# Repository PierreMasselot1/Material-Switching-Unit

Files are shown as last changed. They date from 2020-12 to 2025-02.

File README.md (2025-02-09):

                   

> ⚠️ **This repository has been archived and is no longer actively maintained.** ⚠️
> 
> While the Material Switching Unit (MSU) remains available for reference, please note that:
> - **No new updates, bug fixes, or features will be added.**
> - **Issues and pull requests are no longer monitored or accepted.**
> Use this project at your own discretion, and check the community for alternatives or forks if needed.

# Material Switching Unit (MSU)

The Material Switching Unit is a multi-material upgrade for 3D printers based on the MMU2 that allows printing of up to 5 filaments while staying under 80$ and being compatible with most FDM 3D printers out there.

# Getting started

Clone the repository using the following command (you will need [git](https://git-scm.com/downloads) on your machine)

`git clone --recursive https://github.com/PierreMasselot1/Material-Switching-Unit.git
`

Once this is done you should now have access to the different parts required for this project. The Marlin folder contains the modified firmware that will allow you to control the MSU and the parts forlder contains all the 3D files that you will need.

Have a look at the [build guide](https://github.com/PierreMasselot1/Material-Switching-Unit/blob/main/Build_guide_MSU.md) for further guidance on how to get the MSU up and running!

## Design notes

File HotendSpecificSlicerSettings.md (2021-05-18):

| Hotend Model+Type | E3D V6 (Bowden) | | | | | | | | |
| --- | --- | --- | --- | --- | --- | --- | --- | --- | --- |
| loading speed at the start | 19 | | | | | | | | |
| loading speed | 14 | | | | | | | | |
| unloading speed at the start | 120 | | | | | | | | |
| Unloading speed | 100 | | | | | | | | |
| Number of cooling moves & speed first and last (eg: 1,3,4) | 1,3,6 | | | | | | | | |
| cooling tube position | 40 | | | | | | | | |
| cooling tube length | 7 | | | | | | | | |
| Filament parking position | 70 | | | | | | | | |
| Extra loading distance | 0 | | | | | | | | |
| Important info | Needs Capricorn tubing <br> or PTFE with ID<=1.9mm | | | | | | | | |
| Ramming settings PLA (time: Volumetric speed mm^3/s) | 0.0: 4 / 0.6: 4 / 0.9: 5 / 1.5: 10 / 2: 11 | | | | | | | | |
| | | | | | | | | | |
| | | | | | | | | | |
| | | | | | | | | | |

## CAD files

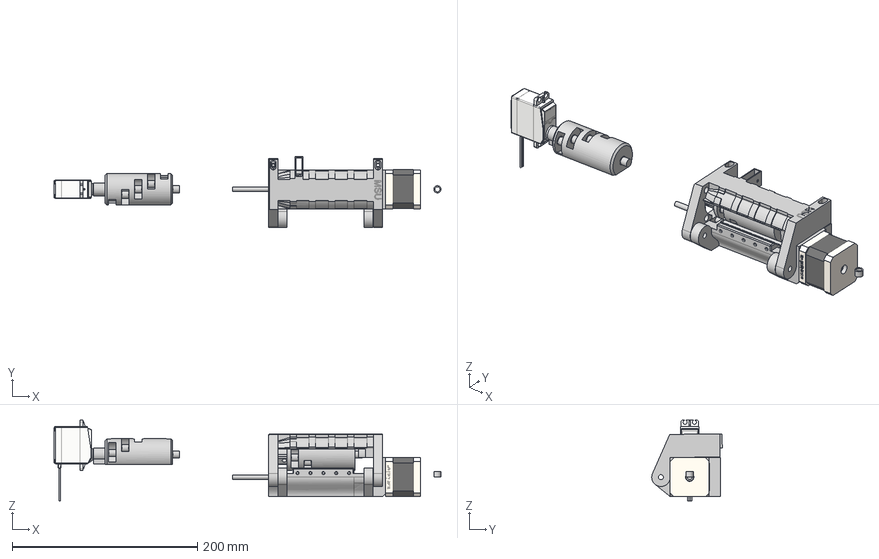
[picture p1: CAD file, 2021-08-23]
parts/STEP/MSU_assembly.step
417.4 x 76.1 x 87.2 mm
pulley body
Idler body stepper
Servo
Idler for servo
bearing adapter
idler stepper motor
Holder nema17 v1

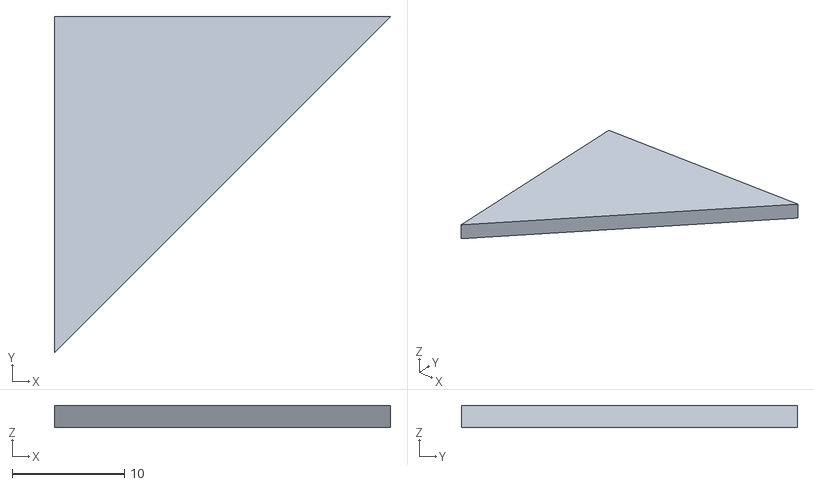
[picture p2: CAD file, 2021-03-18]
FilamentTipTesting/Body1.stl
30.0 x 30.0 x 2.00

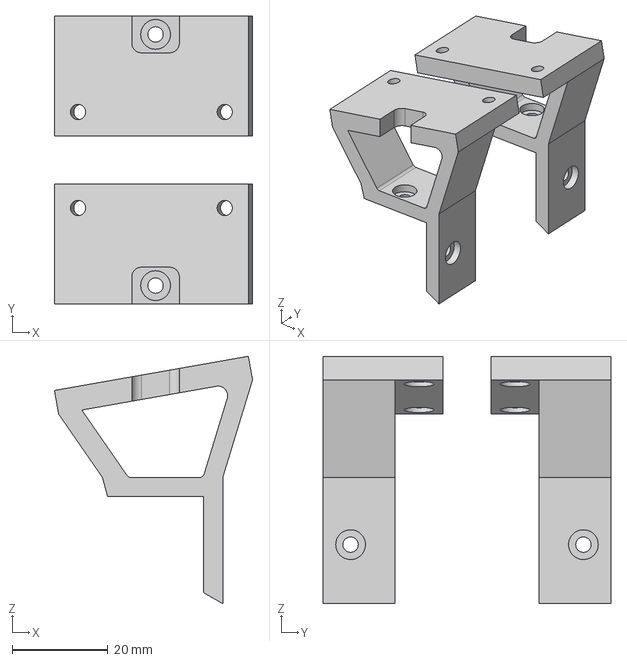
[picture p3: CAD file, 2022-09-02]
parts/STEP/Extrusion_mount.step
41.3 x 60.0 x 51.6 mm

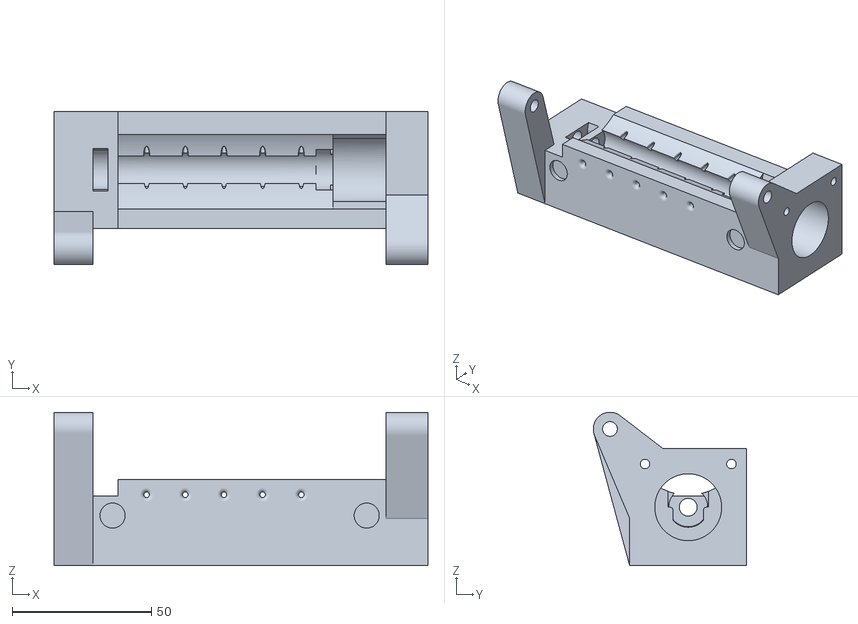
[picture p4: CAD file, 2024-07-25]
parts/STL/Experimental/new_pivot_pulley_body.stl
134.2 x 55.1 x 55.1

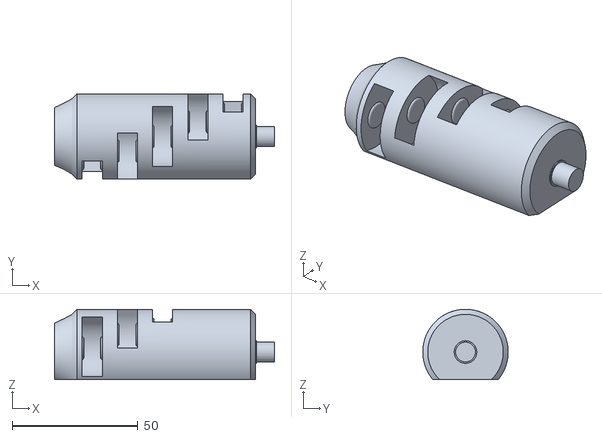
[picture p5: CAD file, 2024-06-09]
parts/STL/Idler.stl
87.5 x 34.0 x 28.0

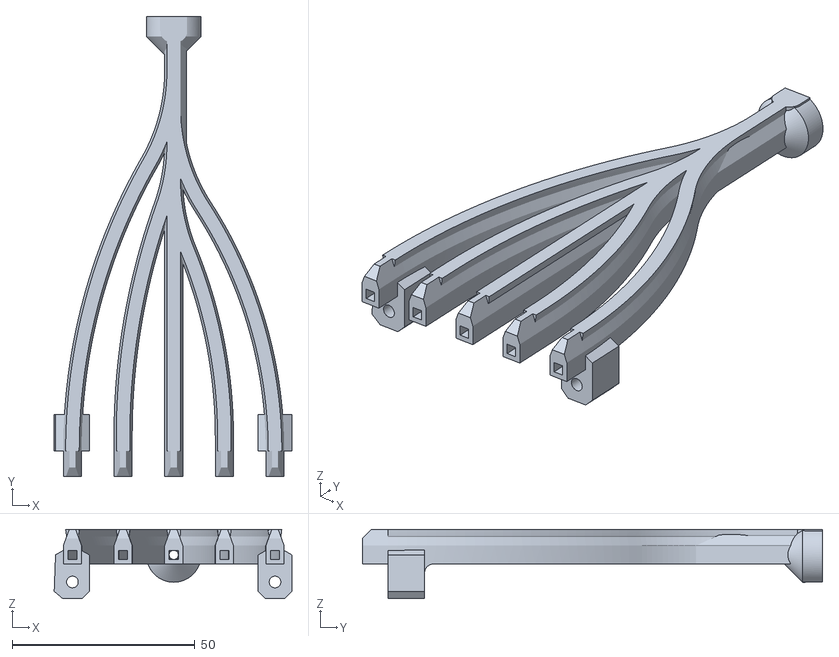
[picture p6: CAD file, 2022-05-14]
parts/STL/Merger/MSU_mounted_merger.stl
65.1 x 126.0 x 19.0

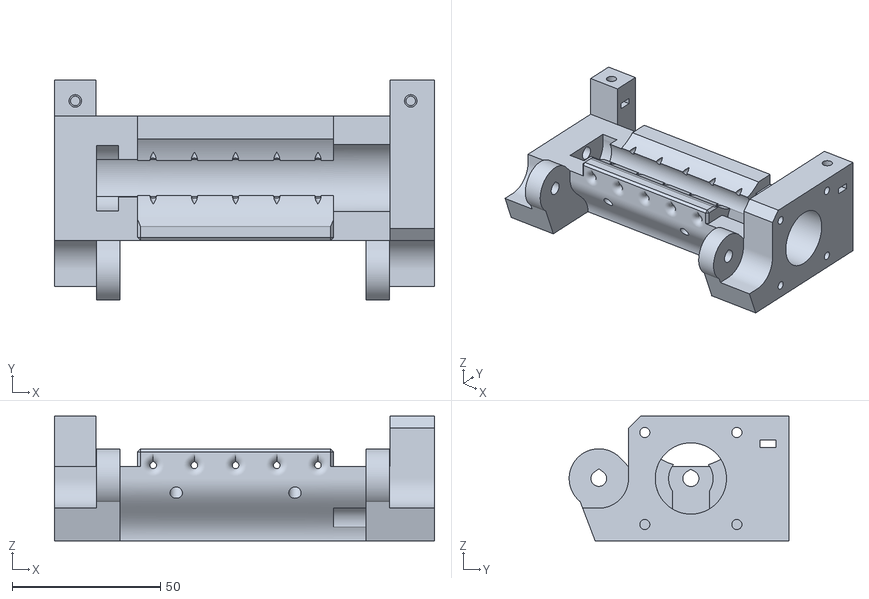
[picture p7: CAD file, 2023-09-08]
parts/STL/Pulley_Body/Downstream_merger_pulley_body.stl
128.0 x 74.0 x 42.0

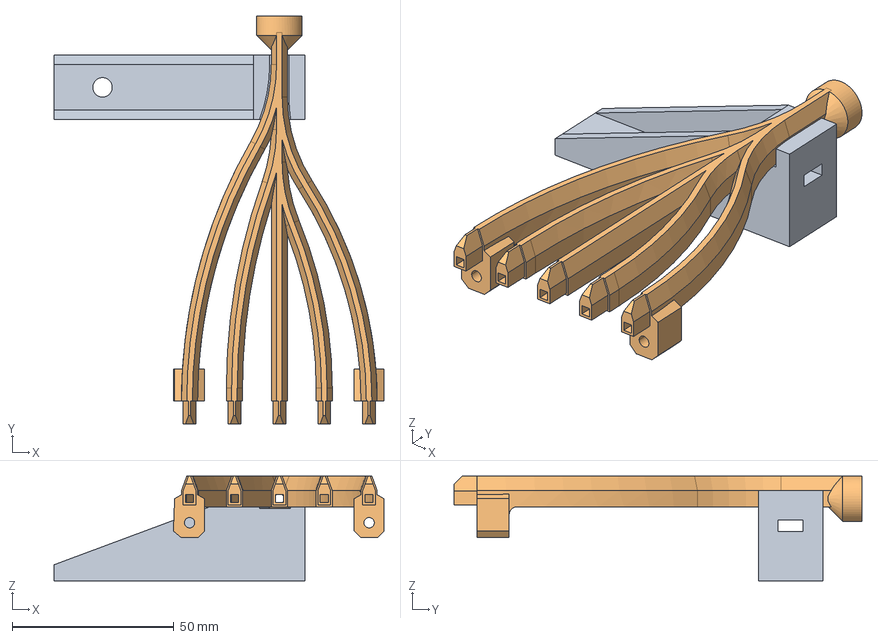
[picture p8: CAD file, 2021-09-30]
parts/STEP/Cube_frame_mount.step
102.0 x 126.0 x 32.4 mm

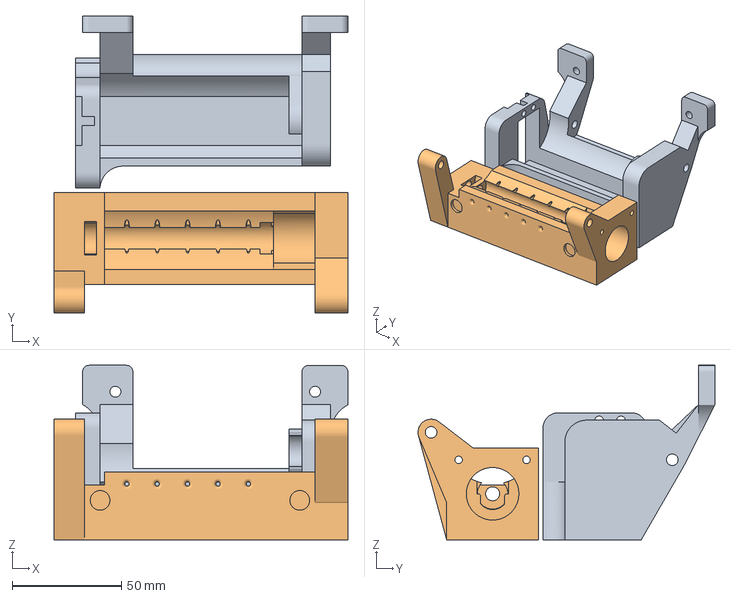
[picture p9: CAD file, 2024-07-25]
parts/STL/Experimental/new_pivot_idler_body.3mf
134.2 x 135.6 x 79.7 mm
new_pivot_idler_body.stl
new_pivot_pulley_body.stl

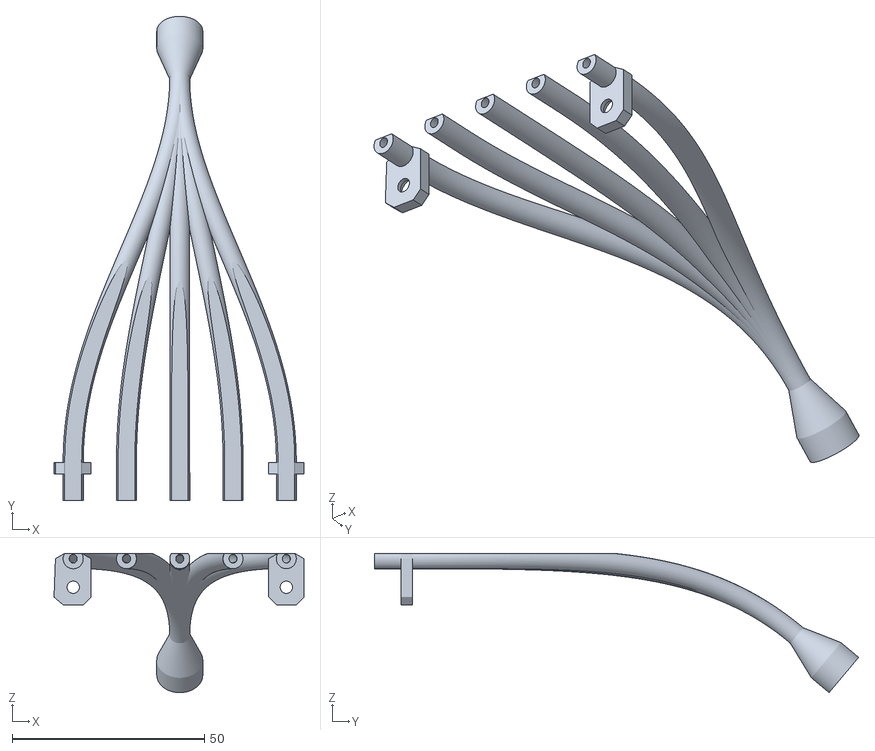
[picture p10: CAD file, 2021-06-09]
parts/STL/Merger/Merger_2.1_Clearance_0.35_mm.stl
65.1 x 126.1 x 36.3

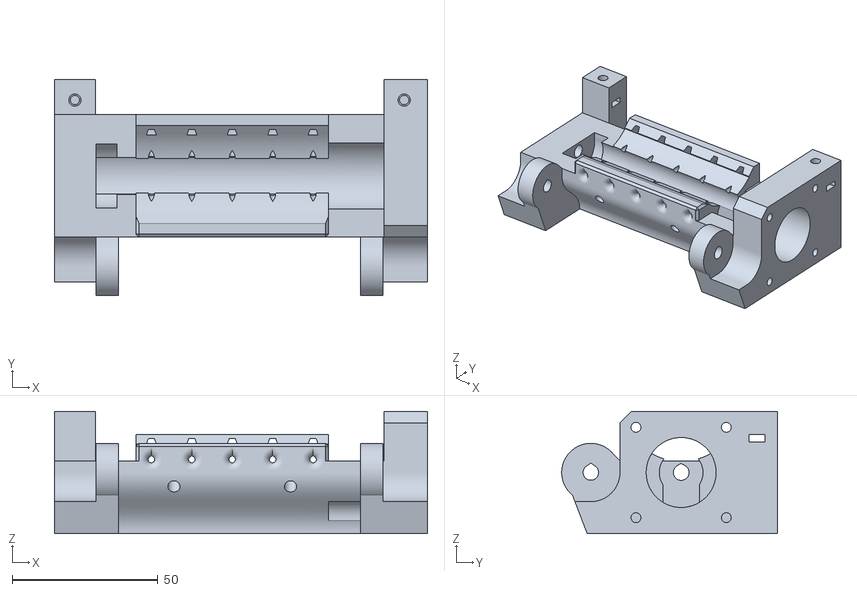
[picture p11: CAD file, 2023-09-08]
parts/STL/Pulley_Body/Direct_mount_merger_pulley_body.stl
128.0 x 74.0 x 42.0

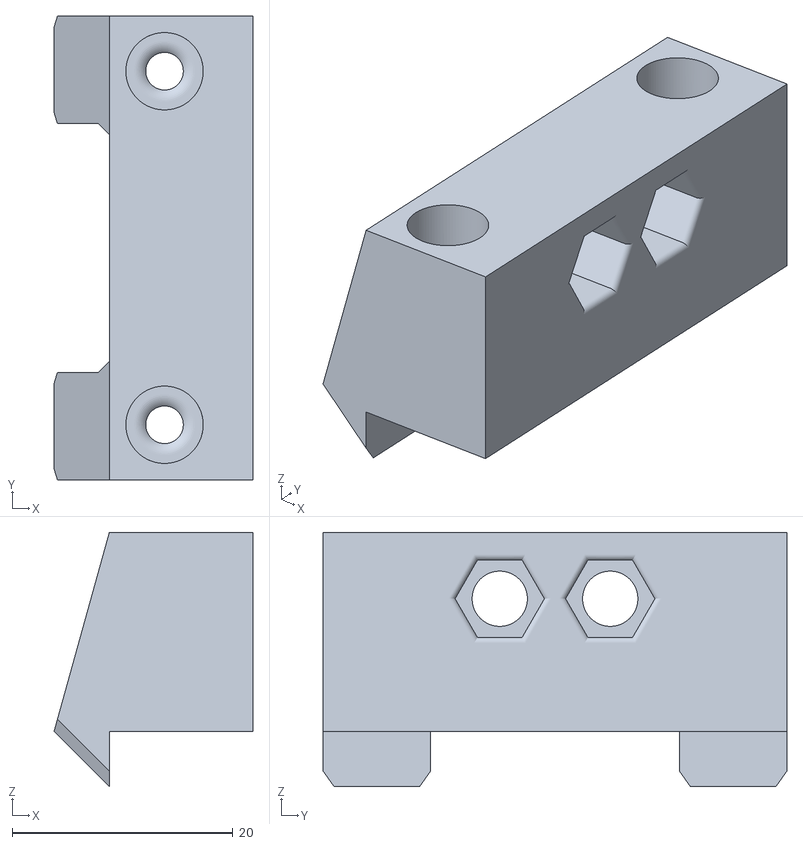
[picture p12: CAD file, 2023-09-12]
parts/STL/Servo_holder.stl
18.0 x 42.0 x 23.0

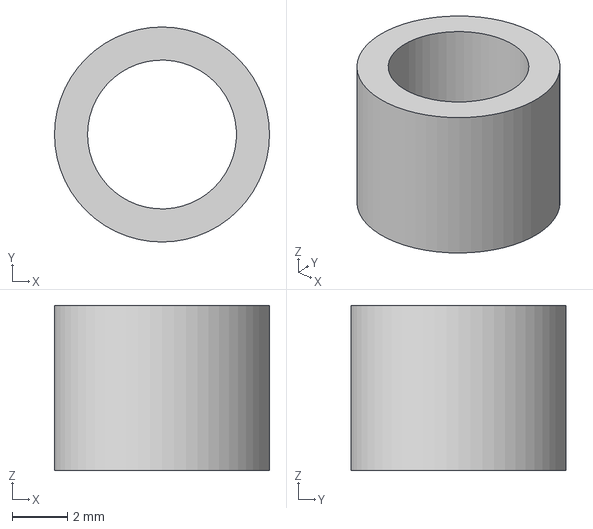
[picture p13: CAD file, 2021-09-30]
parts/STEP/bearing_adapter.step
7.80 x 7.80 x 6.00 mm

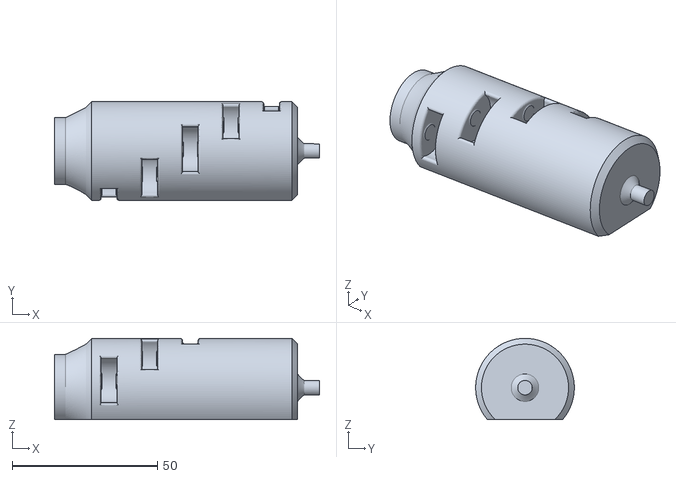
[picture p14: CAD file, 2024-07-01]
parts/STL/Experimental/Idler_605.stl
91.3 x 34.0 x 28.0

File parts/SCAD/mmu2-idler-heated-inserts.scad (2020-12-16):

// PRUSA MMU2
// idler
// GNU GPL v3
// Josef Průša <iam@josefprusa.cz> and contributors
// http://www.reprap.org/wiki/Prusa_Mendel
// http://prusamendel.org

//modified by Pierre Masselot
//fits 608 bearings and embeds the bearings inside the print to avoid any assembly

module idler_segment_l()
{difference(){
    translate([0,0,-9]) rotate([0,90,0]) cylinder(r=11.5, h=8, $fn=50); 
    translate([0,0,-9]) rotate([0,90,0]) cylinder(r=3.95, h=100, $fn=50); }

}
    
module idler_segment_r()
{difference(){
    translate([0,0,-9]) rotate([0,90,0]) cylinder(r=11.5, h=8, $fn=50); 
    translate([0,0,-9]) rotate([0,90,0]) cylinder(r=3.95, h=60, $fn=50); }
 
}

module idler_segment_support(){
     
    {
    translate([8-0.2,0,-9]) rotate([0,90,0]) cylinder(r=11.5+0.8, h=0.4, $fn=50);
    translate([0-0.2,0,-9]) rotate([0,90,0]) cylinder(r=11.5+0.8, h=0.4, $fn=50); 
    difference(){  
     translate([-0.2,0,-9]) rotate([0,90,0]) cylinder(r=11.5+0.8, h=8.4, $fn=50); 
    translate([-0.2,0,-9]) rotate([0,90,0]) cylinder(r=11.5, h=8.4, $fn=50);
        }   }}



module idler()
{

    difference()
    {

    union()
        {
            // base body
            translate([-3,0,0]) rotate([0,90,0]) cylinder(r=17, h=71-2, $fn=50); 
            translate([-5,0,0]) rotate([0,90,0]) cylinder(r2=17,r1=16, h=2, $fn=50); 
            translate([68-2,0,0]) rotate([0,90,0]) cylinder(r1=17, r2=16, h=2, $fn=50); 
            
            // motor shaft coupling
            rotate([-60,0,0]) 
            difference()
            {
                union()
                {
                    translate([-25,0,0]) rotate([0,90,0]) cylinder(r=9, h=20, $fn=50); 
                    translate([-25,-6,5]) cube([20,12,9]);
                    translate([-25,-5,-5]) rotate([60,0,0]) cube([20,16,10]);
                }
                // screws
                translate([-10,0,0]) cylinder(r=1.6, h=12.5, $fn=50); 
                translate([-10,0,4]) cylinder(r=2, h=6.5, $fn=50); 
                translate([-10,0,10.4]) cylinder(r=3.1, h=5, $fn=50); 
                translate([-20,0,0]) cylinder(r=1.6, h=12.5, $fn=50);  
                translate([-20,0,4]) cylinder(r=2, h=6.5, $fn=50); 
                translate([-20,0,10.4]) cylinder(r=3.1, h=5, $fn=50); 
                
                // nuts
                /*translate([-12.8,-2.8,7]) cube([5.6,10,2+0.5]);
                translate([-22.8,-2.8,7]) cube([5.6,10,2+0.5]);
                translate([-12.8,2.8,6.9]) cube([5.6,10,2.2+0.5]);
                translate([-22.8,2.8,6.9]) cube([5.6,10,2.2+0.5]);*/
                
                
                translate([-26,6.5,10]) rotate([30,0,0]) cube([21,16,10]);
            }
        }


    // shaft reinforcement
    difference()
        {
            translate([-21,0,0]) rotate([0,90,0]) cylinder(r=7, h=15, $fn=50); 
            translate([-21,0,0]) rotate([0,90,0]) cylinder(r=6, h=15, $fn=50); 
            translate([-30,-3,15]) rotate([-60,0,0]) cube([30,100,10]);
        }

    // idler bearing segments
    rotate([-160/2,0,0])
    {
    translate([0,0,0]) idler_segment_r();
   
    translate([14,0,0]) rotate([40,0,0]) idler_segment_r();
    translate([28,0,0]) rotate([80,0,0]) idler_segment_l();
    translate([42,0,0]) rotate([120,0,0]) idler_segment_l();
    translate([56,0,0]) rotate([160,0,0]) idler_segment_l();    
    }
    
    // shaft
    difference()
    {
        union()
        {
        translate([-26,0,0]) rotate([0,90,0]) cylinder(r=2.60+0.1, h=25, $fn=50);
        translate([-26,0,0]) rotate([0,90,0]) cylinder(r2=2.60, r1=3, h=3, $fn=50);
        }
        translate([-25,-0.15,5]) rotate([-60,0,0]) cube([20,12,9]);
    }
    
  
   
       
    // shaft bearing

   
  
    
    // endstop cut
    difference()
    {
        translate([8-0.5,0,0]) rotate([0,90,0]) cylinder(r=20, h=6+1, $fn=50); 
        translate([8-0.5,0,0]) rotate([0,90,0]) cylinder(r=14.5, h=6+1, $fn=50); 
        /*difference()
        {*/
            translate([-5,-48,-30]) cube([350,54,50]);/*
            translate([-5,-16,9]) cube([30,30,30]);*/ //should not need that but need testing
        //}
    }
    
    // removal opening
   
    
    // flat bottom
    translate([-30,-25,11]) cube([150,50,15]);
    

    
}}


 translate([-70+2,0,0]) rotate([0,-90,0]) cylinder(r=3.95, h=7, $fn=50); 
rotate([0,180,0]) 
idler();




    
    
    
    
    
    
    

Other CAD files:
FilamentTipTesting/Body2.stl
parts/STL/Idler_body.stl
parts/STL/Mount.stl
parts/F3D/MSU_Assembly.f3d
parts/STEP/MSU assembly.step
parts/STL/Experimental/new_pivot_idler_body.stl
parts/STL/bearing_adapter.stl

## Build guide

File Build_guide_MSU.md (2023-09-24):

# The documentation is not up to date with the latest model revision, while most parts apply some don't  exactly match the currrent models. I will be working on updating it asap but due to finals this might not happen until winter break (aka early January). Thank you for your understanding.

This file is written using the Markdown markup language. If you want to contribute to the documentation and have an easier way to edit Markdown you can use editors like stackedit.io 

## **Multi-material upgrade on any printer: BUILD GUIDE**

The aim of this project is to popularize multi-material 3d printing by making a more reliable, cheaper, and hopefully better multi-material upgrade based on the MMU2 from Prusa. There is still a lot of work to do but this second iteration can be considered as "viable", be ready to put in some work before getting realiable results though!

## **Different setups and compatibility**

information relevant to one specific setup will be preceded by [**setup type**] and ended by [**/setup type**]
ex: 
[**Bowden style version**] information specific to a bowden style setup [**/Bowden style version**]
information relevant for both setups
[**Direct drive version**]information specific to direct drive setups[/**Direct drive version**]

**Bowden style version**
requirements:4 stepper motor controls and drivers(X,Y,Z,E), 1 GPIO pin(servo control) and access to 12V (servo power)

It is the simplest setup, the MSU acts as the extruder and the filament changing process is simple, unload the filament until it clears the merger and then reload the new one by changing the idler position to put pressure on the filament that needs to be used.
This will be compatible with almost every printer and motherboard when using the servo-version.

**Direct drive version**

requirements: 5 stepper motor controls and drivers(X,Y,Z,E,MSU_E), 1 GPIO pin(servo control) and access to 12V (servo power),

This setup is a bit more complicated, it is recommended that you get your setup working in a bowden configuration before attempting this.

**Direct drive version linked extruders**

requirements: servo idler: 4 stepper motor controls and drivers(X,Y,Z,(E and E_MSU combined)), 1 GPIO pin (servo control) and access to 12V (servo power)

This is the same version as the direct drive one with the only difference being that the extruder on both the MSU and the actual extruder will be connected to the same driver meaning that a lot more logic needs to be implemented in order to never have both of them running at the same time, since they have different steps per mm meaning that if we run them at the same time one will be fighting against the other. This setup should be chosen if your board doesn't allow you to run the previous setup, and it is highly recommended that you get your setup working in a bowden configuration before starting this.

## **Before you attempt to build this:**

This guide is currently meant for more advanced user, comfortable with Marlin configuration and with a bit of programming experience. The models may still need work and are not final. You will need to do a lot of tuning before you get everything going, parts modification may be required, and you will almost certainly need to do some troubleshooting. If you are still reading this and want to build this for yourself, I highly recommend you join the discord server (you will find it in the readme file). There is a help channel in there specifically to answer any questions or issues you have while building the MSU.

There are also a few things to know before deciding to build this upgrade. I don’t take any responsibility regarding your actions, this is still a prototype and requires heavy modifications of your printer, which could result in permanent damage, which is a risk that you should be willing to take when attempting this build.

There will also be improvements that may require extra parts in the future, you should be easily able to transition from this version to the newer ones, but this will add extra costs.

Lastly, this is not perfect, and your printer may not work as well as before so you should make sure that you can afford having your printer out of commission and keep a copy of the firmware for single filament on hand (you will work on it later in this guide) so that you can transition back to the original state to print improved parts or to fix models that may not be working correctly.

## **Parts required**

The price total will not match the list exactly since some of those components come in packs of 700 (like screws) when we only need a few and you probably already have them, they will therefore not be part of the total.

The following links were affiliate links, amazon closed the affiliate account since I probably don't have enough subscribers for it. I will hopefully be able to get those back soon enough.

| Part name | Picture | Links | Pcs in pack | Pcs needed | Price $ |
|--|--|--|--|--|--|
| 608 ball bearings| 608 ball bearings |[https://amzn.to/3ePrE0i](https://amzn.to/3ePrE0i)<br />[https://aliexpi.com/Ep3X](https://aliexpi.com/Ep3X)|10|6|5.17$|
|Heated inserts M3||[https://amzn.to/3ogq3nt](https://amzn.to/3ogq3nt)|100|~10|10$|
|M3 and M2 bolts and nuts| |[https://amzn.to/3bu7WVL](https://amzn.to/3bu7WVL)|700|~20|20$|
|PTFE tubing<br/> PC4-M10<br/> PC4-M6||[https://amzn.to/2RWcyNH](https://amzn.to/2RWcyNH)<br/>these type of kits include everything you will need(and much more with the new merger) and are the best value|5m<br/>10 pcs<br/>10 pcs|0.5m<br/>1 pcs<br/>1pcs|10$|
|5mm to 5mm coupler||[https://amzn.to/3ou1XG1](https://amzn.to/3ou1XG1)<br/>[https://amzn.to/3ybPWcp](https://amzn.to/3ybPWcp)<br/>In a last resort situation you can opt of the flexible 5 to 5 couplers that are more commonly available, but definitely replace it with a solid coupler ASAP|2|1|7$|
|Metal rod 5mmx124mm (a little longer won’t cause any problems and you will have a hard time finding a rod exactly to size)||[https://amzn.to/3btXOMH](https://amzn.to/3btXOMH)<br/>[https://amzn.to/3tSTv3Y](https://amzn.to/3tSTv3Y)<br/> Following links are for a D shaft, basically a rod with one side machined in order to be able to easiely secure and mount the gears. (making a D shape, hence the name)<br/>Similar results can be optained by using a dremel to flatten the rod at each set screw position<br/> https://aliexpi.com/Zrzg|5<br/>|2|8.5$|
|MK8 gears with filament groove||[https://amzn.to/3uQZVlo](https://amzn.to/3uQZVlo)|5|5|8$|
|Nema 17 stepper motor||[https://amzn.to/3wy6Gcv](https://amzn.to/3wy6Gcv)<br/>needed for direct drive or if original extruder doesn't use a regular sized NEMA 17 stepper motor|1|1|14$|
|Servo|(https://postimg.cc/3dRbgSxy)|https://amzn.to/3bQh1sd </br> https://www.amazon.com/Seamuing-Aluminum-Futaba-Mechanical-Helicopter/dp/B07D56FVK5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</br><br/> You might also need a coupler if it's not included. </br></br>Make sure your servo has 270 degrees of range or more (anything above 200 should work but current setup is being developed and tested with a servo that has 270 deg of range), and make sure that is is not a continuous servo (be careful when looking at 360 degree servos because these tend to be continous)</br>|1|1|17$|
|Idler springs|idler springs|[https://shop.prusa3d.com/en/spare-parts/599-idler-spring.html](https://shop.prusa3d.com/en/spare-parts/599-idler-spring.html) <br/>[https://www.voxelfactory.com/collections/original-prusa-i3-mk2-mk2s-parts/products/replacement-tension-spring-for-prusa-i3-mk2s-or-mk3](https://www.voxelfactory.com/collections/original-prusa-i3-mk2-mk2s-parts/products/replacement-tension-spring-for-prusa-i3-mk2s-or-mk3)<br/>(next links are not originial prusa springs but match the specs closly and will work perfectly fine)<br/>https://amzn.to/3hKlO2d <br/> https://aliexpi.com/HHM1<br/>You will want to choose 10mm length 0.9mm wire diameter and 5mm outer diameter|1|2|4-8$|
| | | [**Direct drive version**]<br/>for the direct drive version you will only need one extra stepper motor, see NEMA 17 stepper above[**/Direct drive version**]||||
| | |[**Direct drive version linked extruders**]<br/>for this version you will also need  the extra stepper driver but also a stepper motor splitter linked below[**/Direct drive version linked extruders**]||||
|Stepper parallel module|(https://postimg.cc/SjM12xyp)|https://amzn.to/3hNCplH|3|1|8$|
|total bowden |||||78$|
|total direct drive|||||83$|
|total direct drive linked extruder|||||91$|

## **Prebuild checks**

[**Direct drive version**]

The first thing you should do is to find some way to feed the filament to the extruder using a bowden tube, you will most likely have to design an adapter to be able to fit a PC4 M6 or M10 coupler on there. I will try to have as many of those in the GitHub repo but you may have to design it yourself. If you do end up designing one make sure to add it to the repo so that other people can use it (you can do so by creating a pull request). If you don't know how to or don't want to spend the time designing one shoot me a pm on discord and I could design one for you setup in exchange for  a small commission.

You will also need to make sure that your extruder assembly can easily grab filament with minimum pressure applied. Since we need to change the filament multiple times during the print, the extruder gears need to be able to grab onto the filament and feed it to the nozzle without any clogs or jams. To test this you can simply go inside motion in Marlin and extrude a long distance, and while the extruder is running slowly insert the filament into the extruder. The pressure required for the filament to be grabbed by the gears should be minimal and once grabed the filament should be able to be fed up to the nozzle without any clogging or jamming. If the filament is not bein grabbed by the gears, you may need to reduce the extruder idle pressure by slightly shortening the spring (proceed at your own risk! this has a high chance of messing up your extruder and you will most likely end up needing to order a new extruder spring) if the filament is being grabbed by the gears but is not feeding correctly up to the nozzle its most likely because there are some gaps in the assembly where the filament can escape and cause jams. To fix this you will have to get creative but some modifications for your specific extruder probably already exist because printing with super flexible filaments has similar requirements. These modifications will most likely involve lining as much as the filament path with PTFE tubing. Finally, some extruders may simply not work very well for the MSU and you may have to switch to a known compatible extruder (I will work on a list of compatible extruders at some point in the future)

 [**/Direct drive version**]
 
Before trying to build this upgrade, you should have a fully working printer, with a compatible mainboard (check below), with Marlin configured properly for a single extruder. You should get the Marlin source code from the Marlin fork that is inside the repo, it is currently a submodule of this repo so you will have to clone it independantly. Once you have Marlin configured for your printer before upgrading to the MSU keep a copy in a known location so that you can easily transition back to stock if the upgrade where to fail. 

After that, download the latest version of PrusaSlicer or SuperSlicer and follow this guide ([https://www.youtube.com/watch?v=Wz2Soog4HkQ&t=245s](https://www.youtube.com/watch?v=Wz2Soog4HkQ&t=245s) ) on how to set everything up for your printer in a single extruder mode. 

Once all off that is done download the latest files from this repo and start printing them using the methods and settings mentioned below. Check that you also have all the components and tools required.

## **Motherboard compatibility**

Your motherboard will need to have all the ports required for the specific setup to choose. One extra thing to keep in mind is that you will need a splitter if you have a double Z axis. This is probably already integrated into your mainboard but if not those can be bought easily(same part as the splitter in the BOM). If your motherboard is not compatible with the setup that you wanted to build changing motherboard is an easy process and you can find board like the SKR 1.4 turbo for pretty cheap. If you are looking for a boar specifically for this setup something like the SKR PRO is ideal as it has a lot of stepper motor controls and expansion capabilities.

## **Printing**

The STL files can be found in this repo. They are also available on thingiverse, search for MSU and you will have everything you need. Most parts can be printed at 0.2 mm with a 30% infill and without supports. The merger needs supports touching build plate and should be printed with a 0.1 mm layer height and at least 50% infill, with 100% being preferable.

## **Idler**

The following slicing instrcutions are for PrusaSlicer and SuperSlicer. This is a good time to download SuperSlicer(PrusaSlicer would also work but since SuperSlicer has more multi-material related features this is what we are going to be working with).

The idler prints vertically like shown below:

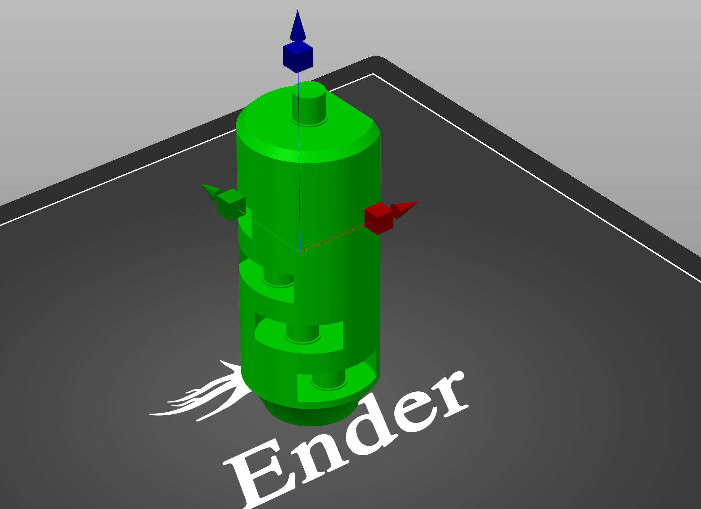
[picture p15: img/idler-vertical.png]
idler


You can then slice the idler using a layer height of or under .2mm.
The parts needs multiple pauses in the print, this allows for the insertion of bearings before restarting the print.

In order to insert a pause at a specific layer you will first need to slice your model, then, in the sliced preview, you will use the slider on the right side to place yourself on one of the top layers of one bearing slot.

You will then find the exact layer where the shaft increases in diameter using the up and down arrows to move by one layer at a time, and insert a pause on the last layer with the regular shaft size.

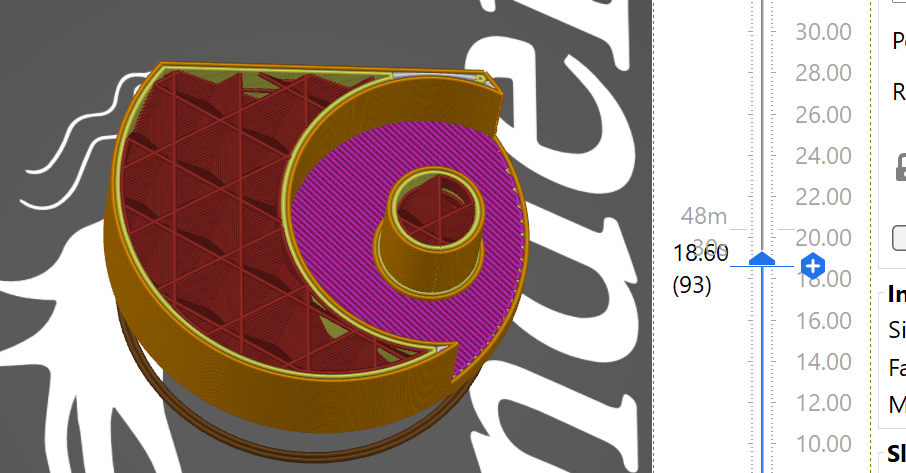
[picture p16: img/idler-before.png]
idler before shaft size increase


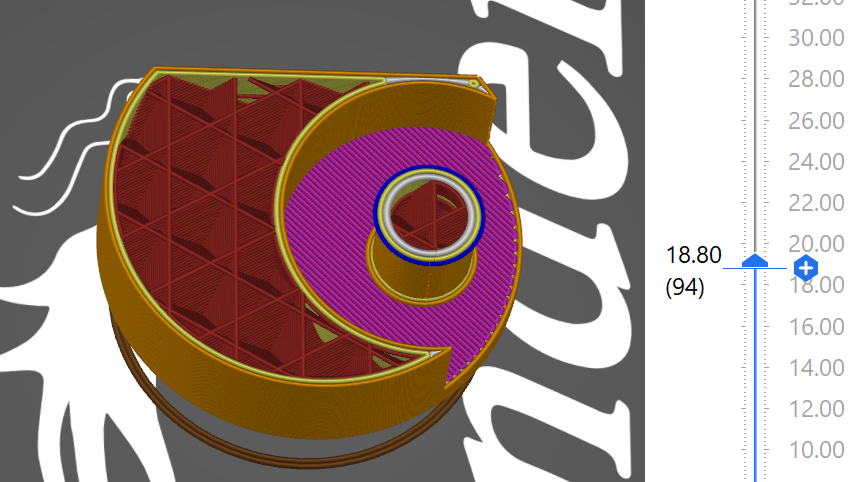
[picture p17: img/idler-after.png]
idler after shaft size increase


In this case the pause script will be inserted on layer 93. To insert that pause you will want to put the slider back at that position using the arrows and **right** click the little plus icon on the right of the slider.

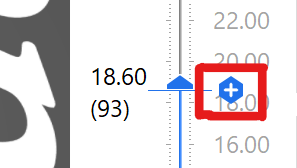
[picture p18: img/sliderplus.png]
slider plus option


After right clicking that button you will see multiple options and one of those being add custom Gcode, click on the custom Gcode option. Enter the following Gcode commands in the text field that appears:

	G0 X0 Y0

	M104 S0 ; standby temperature

	M0 ; Do the actual pause

	M109 S200 ; resume temperature you may need to change that value to match the material you are using

Pausing scripts can be a bit of a pain depending on your printers manufacturer. A bit of googling should hel you find adequate gcode, the previous snippet is what has been the most sucessful in my case.

## **Merger**

The merger is one of the hardest parts to print due to it's low contact surface. Make sure that your bed is well leveled, and that you don't have any supports inside the tubes and you should be good to go. (This is one of the parts that I will rework to allow for easier printing).

## **Assembly:**



You will then need to setup your motor. Connect the motor and one of the 5mm metal rod. If you are using a flexible coupler, make sure that the two ends are touching to reduce flex to a maximum. Slide all the extruder gears onto the rod but do not tighten them too much yet: the screws used are really small and can be damaged easily and you will need to be further in assembly in order to align the gears properly.



The next step will be to insert heated inserts in all of the parts that need them. The following images show those locations.

Pulley body:

Just note that for this next picture the heated inserts are optional and can be replaced by M3 nuts (less stylish but will perform better in the long run).
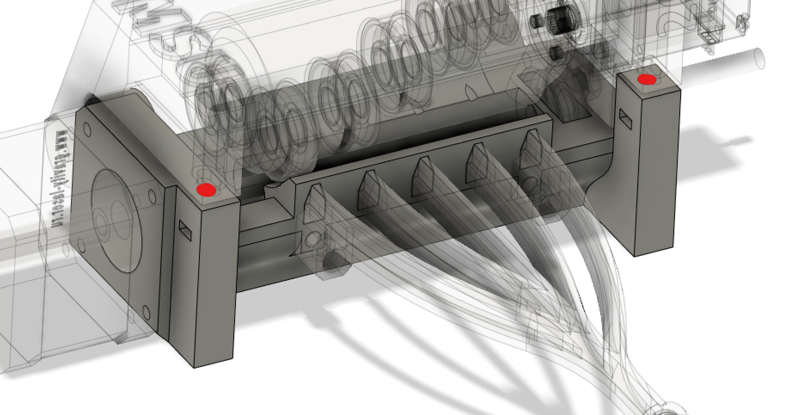
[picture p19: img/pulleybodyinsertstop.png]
heated inserts top of pulley body


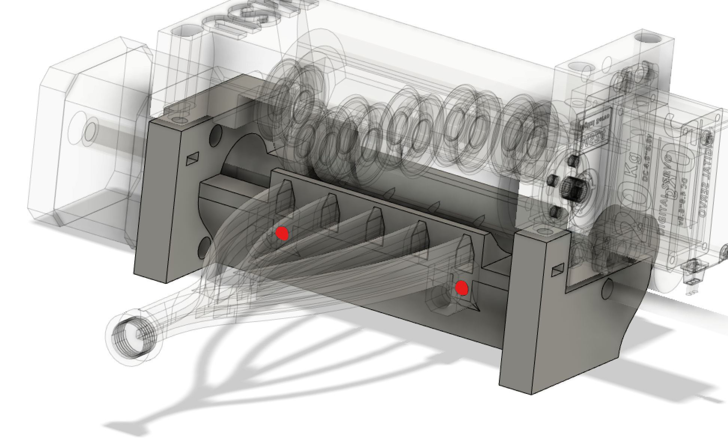
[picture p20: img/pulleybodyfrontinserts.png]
heated inserts front of pulley body


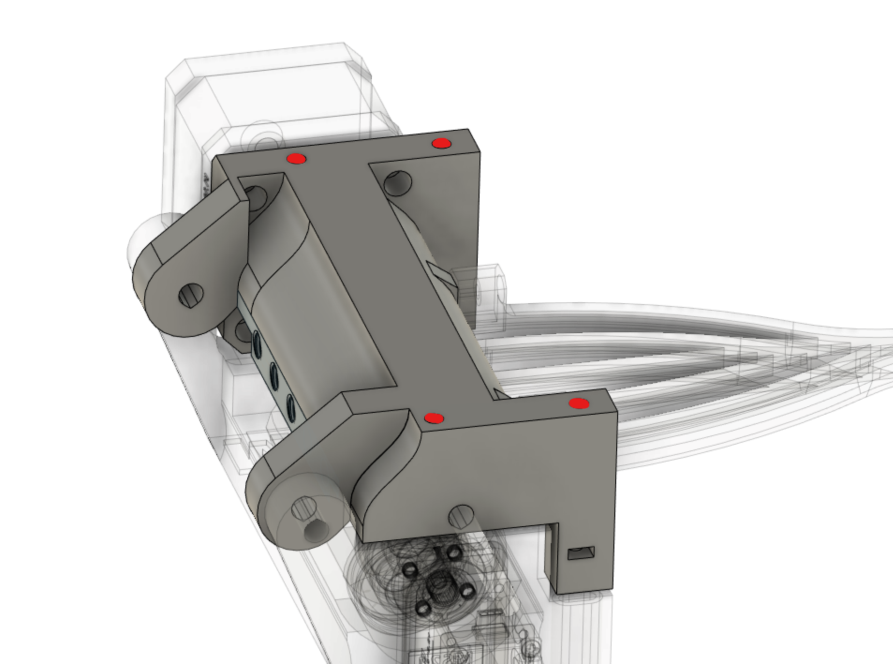
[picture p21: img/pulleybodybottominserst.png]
heated inserts bottom of pulley body


Idler body:

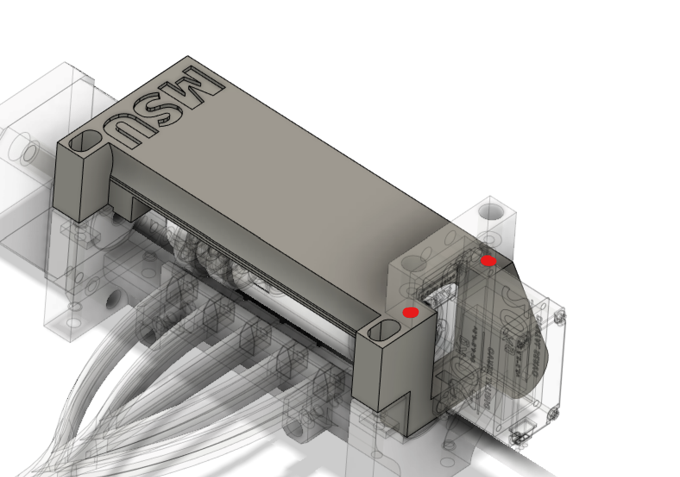
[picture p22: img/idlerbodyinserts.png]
heated inserts bottom of pulley body


If you are not familiar with heated inserts here is a guide: [https://hackaday.com/2019/02/28/threading-3d-printed-parts-how-to-use-heat-set-inserts/](https://hackaday.com/2019/02/28/threading-3d-printed-parts-how-to-use-heat-set-inserts/)

They are not that difficult to use just make sure to not heat up your part for too long.



You can then insert the motor and shaft assembly. Secure the motor using M3*8 screws. You can now align each of the gears with the filament slot corresponding and properly tighten them. If you see that your gears are sliding onto the rod you can use a Dremel to flatten a spot for the set screw, this will help a lot and works much better than simply trying to tighten everything more as you won't risk damaging the threads.



Place a bearing on the end of the idler and pass it through the motor hole of the idler body. You will then be able to press fit it in the dedicated slot.



Once inserted use M4 screws to secure the servo to the idler body. Don't bother tightening them much at this point since you will need to re align the idler once the firmware is flashed.





Assemble the idler body and pulley body as shown and insert the remaining metal rod through the dedicated holes.



The amount of force required to insert the rods may vary depending on your print settings but I still need feedback regarding clearances so if you have a well calibrated printer let me know whether the clearances are right or whether I need to increase/decrease them.



You can now insert the spring and the screws: M3x(from 25 mm up to 35 mm) in order to tension the idler. For now idler tension will be made through trial and error but a good indicator is when you are able to open idler slightly and that the springs push it back in a closed position. I will add visual indicators in a later model once we have found a cheap, widely available spring that works well with the MSU.



You will then need to mount the MSU to your printer. A mount is included in the 3D files and it fits onto 20 by 20 extrusions, you will just have to print the proper nuts in order to attach it to the extrusion. If this mount doesn't work with your printer you can design and share your own.
### Connecting the Merger
Insert the merger inside the pulley body (the fit should be a press fit), and secure it in place using 2 M3x8 mm. You can now connect the PTFE tube from the output of the merger up to the nozzle. Make sure that the PTFE tube is going inside it's dedicated slot inside the merger (and not simply into the coupler), if there are clogs with regular filament (1.75mm that hasn't been inside the nozzle) inside the merger try with and without the coupler. If it doesn't  jam without the coupler it means that the PTFE tube was not properly inserted. If it jams in both cases it means that your clearances a probably off, try increasing the scale of the model.

You are now done with the building process.

## **Marlin configuration**

This needs to be done **after** you have successfully configured Marlin for a single extruder setup.
It is recommended that you work off off a branch of my Marlin branch, this will help you get any update I do to the codebase without having to reconfigure Marlin. This is particularly usefull in our case since this is a work in progress and things are bound to change. If you know how to use git and github this shouldn't give you any problems but in case you are not familiar with how everything works the following links are resources to get you started

Getting started with GitHub Desktop: https://docs.github.com/en/desktop/installing-and-configuring-github-desktop/overview/getting-started-with-github-desktop
How to fork a repository: https://docs.github.com/en/desktop/contributing-and-collaborating-using-github-desktop/adding-and-cloning-repositories/cloning-and-forking-repositories-from-github-d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
How to keep your fork up to date with the original repo: https://docs.github.com/en/desktop/contributing-and-collaborating-using-github-desktop/keeping-your-local-repository-in-sync-with-github/syncing-your-branch
And make sure that you configure Marlin using my branch of Marlin, if you use the original one you won't have access to the following settings.

The following code snippet are the MSU related settings inside the Configuration.h file (Marlin/Marlin/Configuration.h)

This line needs to be uncommented in order to enable MSU functionalities
```cpp 
#define MSU
```
The following lines of code are responsible for the selection of the type of setup you want to run. Choose one between bowden, direct-drive, and direct-drive with linked extruders. On top of that you have the option to use a servo controlled iderl, the default being a stepper-controlled idler
```cpp
#if  ENABLED(MSU)
//#define MSU_BOWDEN_TUBE_SETUP //enable when using a bowden style setup
//#define MSU_DIRECT_DRIVE_SETUP //enable when using a direct-drive setup
//#define MSU_DIRECT_DRIVE_LINKED_EXTRUDER_SETUP //enable when using a direct-drive setup using a single driver for both the MSU and the extruder
```
The following lines are additional configuration options that are most likely already good but that you want to double check in case you have a different setup. Use the description to understand what each setting does and adjust them accordingly if need be.

One thing that you will more than likely have to do is adjusting the servo angle so that it aligns properly with each filament slot. Here is how to do it:

Before attaching the idler to the servo, power up the printer and use the MSU menu (or the Gcode command T0, T2,..., T4) to move the idler to each filament position. Each time, use the M280 Gcode command to read the corresponding servo position and write them down.  Once this is completed, set the idler to the position for the first filament (or use the Gcode command T1).  Attach the idler to the servo, ensuring that the position of the  bearing for filament 1 is aligned with the first extrusion gear. You might not be able to get that alignment perfect at this time due to the way the servo and idler are coupled, this is not a problem since this can be fine tuned at a later stage, just get it "close enough". Once the idler is attached to the servo, use the M280 command to position the idler drum "perfectly" for filaments 1 and 5, noting the angle setting for each "perfect" setting. If need be you can subtract the position 1 to the position 5, divide it by 4 and you will obtain the proper value for MSU_BEARING_ANGLES (the defaults should be close but if you modify the idler for example ths will allow you to get an accurate value for your setup). You should have one initial angle for the first filament and one adjusted angle(first and second steps), set the MSU_SERVO_OFFSET setting in the firmware to the difference between the two.

If this is a bit confusing... well that's because it is. If you aren't able to get good alignment try to do small adjustments and re-flashing the firmware  until you get the idler to align with each filament.

```cpp
#define MSU_MENU//LCD Menu

#define MSU_SERVO_IDLER_NBR 0 //define the servo motor number
#define MSU_SERVO_OFFSET 0 //defines the offset in degrees for the idler, this can be used to fine tune idler alignment
#define MSU_BEARING_ANGLES 26 //defines the angle from on ball-bearing to the next on the idler
#define MSU_SPEED 25 //unload and load speed of the MSU in mm/s, fine tuning can be done from the slicer
#define MSU_EXTRUDER_NBR 0 //define the MSU extruder motor number (as setup in your board pins file)
#define MSU_PARKING_POSITION 270 //define angle of the servo for the parking position

#if ENABLED(MSU_DIRECT_DRIVE_SETUP)
	#define MSU_ORIGINAL_EXTRUDER_NBR 2//define the extruder nbr that the actual extruder is connected to 
#endif

#if ENABLED(MSU_DIRECT_DRIVE_LINKED_EXTRUDER_SETUP)
	#define MSU_EXTRUDER_STEPS_PER_MM 120 //steps per mm of the MSU, should not require any tuning. Necessary since we are using a single driver with motors that potentially have different steps per mm
#endif

```
The two next lines are to set the length of the bowden tube and of the distance from the nozzle to the extruder gears (only required for direct drive)
```cpp
 #define MSU_BOWDEN_TUBE_LENGTH 600 //length between MSU and the nozzle or from the MSU to the extruder gears (for direct drive setups)
 #define MSU_GEAR_LENGTH 40 //for direct drive setups only, amount of retraction needed to disengage the filaments from the extruder gears

#endif 
```

Remember to set your extrude_maxlength higher than your bowden tube length
```cpp
/**
* Prevent a single extrusion longer than EXTRUDE_MAXLENGTH.
* Note: For Bowden Extruders make this large enough to allow load/unload.
*/
#define  PREVENT_LENGTHY_EXTRUDE
#define  EXTRUDE_MAXLENGTH  200
```
You will also need to define driver type for each motor(should already be the case but make sure to add stepper driver type if ou are using an extra motor for the MSU)

```cpp
#define  X_DRIVER_TYPE A4988
#define  Y_DRIVER_TYPE A4988
#define  Z_DRIVER_TYPE A4988
//#define X2_DRIVER_TYPE A4988
//#define Y2_DRIVER_TYPE A4988
//#define Z2_DRIVER_TYPE A4988
//#define Z3_DRIVER_TYPE A4988
//#define Z4_DRIVER_TYPE A4988
#define  E0_DRIVER_TYPE A4988
//#define E1_DRIVER_TYPE A4988
//#define E2_DRIVER_TYPE A4988
//#define E3_DRIVER_TYPE A4988
//#define E4_DRIVER_TYPE A4988
//#define E5_DRIVER_TYPE A4988
//#define E6_DRIVER_TYPE A4988
//#define E7_DRIVER_TYPE A4988
```
Similarly to your XYZ axis you can change the direction of the extruder stepper in order to match the expected behavior. If the idler goes in the opposite direction you would change E1 dir to false(Or E x if you have setup custom extruder pins)
```cpp
// For direct drive extruder v9 set to true, for geared extruder set to false.
#define  INVERT_E0_DIR false
#define  INVERT_E1_DIR false
#define  INVERT_E2_DIR false
#define  INVERT_E3_DIR false
#define  INVERT_E4_DIR false
#define  INVERT_E5_DIR false
#define  INVERT_E6_DIR false
#define  INVERT_E7_DIR false
```

Also don't forget to have NUM_SERVO parameter defined to the number of servos you are running (at least one for the idler)

```cpp	
#define NUM_SERVOS 1 // Servo index starts with 0 for M280 command
```	

If you need to use multiple servos on motherboard or if your motherboard isn't pre configured to support servos, the following tutorial will be useful. This is specifically for the SKR V1.4 but the process is similar for other boards (just make sure to edit the correct pins file).

<a href="http://www.youtube.com/watch?feature=player_embedded&v=E4N4GjqYsy4
" target="_blank">IMAGE ALT TEXT HERE</a>

### Direct Drive Setup
Additionally if you are building the MSU for a direct drive setup you will need to define an additional extruder (only for the non-linked version). To do so increment the number of extruders in Configuration.h
```cpp
#define EXTRUDERS 2
```

You will need single nozzle to be enabled by uncommenting the following line in Configuration.h
```cpp
#define SINGLENOZZLE
```

You might also need to update the pins file on your board if it does not support dual extruders natively.

You are now done with the software modifications.
**if at any point you are seeing unexpected behavior it is recommended to connect your printer to your computer and use something like pronterface in order to get more debugging info through the serial communication**

## **Slicer settings.**
The pictures are for PrusaSlicer but as of now I recommend using [SuperSlicer](https://github.com/supermerill/SuperSlicer/releases) which offers better multi-material capabilities. The picture are still relevant as the UI is pretty much the same. Will be updating them shortly.

You will now need to configure the slicer in order to adapt it to your printer.

You can use the same slicer profile that you were using or create a new one (recommended)

The first thing you will need to do is change the number of extruders to 5, in the printer settings tab and to check the single extruder multi material



You also need to use relative E distance

You should now have 5 extruders to work with.

In there you can change retraction settings, this might need to be a bit higher than before but 10mm is on the really high side of things. Just pick the smallest value that doesn't give you too much stringing.



Now go to the single extruder multimaterial parameters(Single extruder MM setup)

You will have four things to adjust. First off, the cooling tube position. In order to find it simply measure from your nozzle to the middle of the cooling block on your extruder. The cooling tube length will vary depending on your extruder but 10mm seems to be a good value for most extruders. The filament parking position should be the cooling tube position+ (the cooling tube length/2) since we are handling the unloading and reloading in Marlin (may not be as necessary right now but when working with less capable boards will enable us to make some really interesting stuff…  more info on that later) the extra loading distance should be at 0 and be tweaked if you find that it doesn’t start extruding exactly when restarting (this is irrelevant when using a wipe tower).



You will then go in filament settings and make sure that you have keep fan always on turned on since it will stop when doing tool changes and not turn on for small patches of color.



This is where SuperSlicer varies and comes in with a lot more options. Got to the multi-material tab and this is where you will find a ton of options. I personally haven't  had enough time to do advanced comparative testing on all of them so the process is still trial and error but I will try to sumarize what every option is. Extra info is also available directly in the slicer, just hover your mouse over a specific setting and it will give you a detailed summary of what that option does.
SuperSlicer
So the first section that you can see is the toolchange temperature. This allows you to drop the temperature in order to reduce stringing while still being able to print at the temperature you usually use. The fast mode and cooling fan options are self explanatory(just know that fast mode will not wait for the hot end to reach the specified temperature but try it's best to reach it in time). You then have the skinny dipping menu which allows you to dip the filament back into the meltzone after extraction in order to reduce stringing. Start with a low insertion distance and increase until stringing dissapears. Also notice that this setting will be impacted by the cooling tube position so any change on that will also impact the required insertion distance.

The next settings are also part of PrusaSlicer, you can adjust the filament change time in order to get more accurate time extimates for your print. I recommend you measure the tool change time for your setup by sending T1 or any toolchange gcode and measure the time that it takes. This setting is very usefull since leaving it at 0 will give you some extremly optimistic results and on a 15 hr print it may be off by up to two hour, and this can result in lack of sleep...don't ask me why.
The last thing in there that your will need to adjust is the ramming setting. The default one seems to work but with a bit of tweaking you can get a way cleaner filament tip the following picture is an example of what I \*was\* running (settings all over the place right now but will share once I have good results) but you will need to do a bit of experimenting on your side.



You just need to click on ramming settings to get access to these controls.

In print settings make sure that you have the wipe tower enabled inside of the Multiple extruder tab and prime all printing extruders enabled as well.



You are now done with slicer settings.

To print you will just need to import a multicolor model. Launch prusa slicer, open all the parts of your model at the same time.



Click open



Hit yes

You will then be able to select different extruders on the right hand side of your screen. Happy printing!

If you have any problems, make sure to message me on discord so that I can both help you and improve the documentation.

## **Tips to get a successful multicolor print.**

Idler tension is key to get good prints. If you see any extrusion discrepancies or under extrusion, then the fix will most likely be to increase idler tension.

If a specific filament gives you more trouble than the other create a profile specifically for it that is more aggresive and takes up more time but gives better result (have a slower BAD FILAMENT profile)

Another failure point that I have seen is on the coupler and the gears, if they are not tight enough, they will slip on the rod, resulting in under extrusion or even no extrusion in some cases.

The purge block is a huge waste of filament, but it can be adjusted based on the filament transition (transitioning from blue to cyan will require less purging that from black to white). Other things like wipe in object and wipe in infill can be enabled an optimized in order to reduce filament waste.

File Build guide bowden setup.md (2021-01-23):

This file is written using the Markdown markup language. If you want to contribute to the documentation and have an easier way to edit Markdown you can use editors like stackedit.io 

**Multi-material upgrade on any printer: BUILD GUIDE**

The aim of this project is to popularize multi-material 3d printing by making a more reliable, cheaper, and hopefully better multi-material upgrade based on the MMU2 from Prusa. There is still a lot of work to do but this is prototype that works well enough to be considered as viable.

**Before you attempt to build this:**

This guide is currently meant for more advanced user, comfortable with Marlin configuration and with a bit of programming experience. The models may still need work and are not final. You will need to do a lot of tuning before you get everything going, parts modification may be required, and you will almost certainly need to do some troubleshooting. If you think this is too much for you do not worry, I will be releasing a tutorial that goes way more in depth and should be easier to follow, the models shown and provided in this video will be tested on multiple printers and the risk of something not working will be reduced by a lot. If you are still reading this and want to build this for yourself, I highly recommend you join the discord server. There is a help channel in there specifically to answer any questions or issues you have while building the MMU.

There are also a few things to know before deciding to build this upgrade. I don’t take any responsibility regarding your actions, this is still a prototype and requires heavy modifications of your printer, which could result in permanent damage, which is a risk that you should be willing to take if attempting this build.

There will also be improvements that may require extra parts in the future, you should be easily able to transition from this version to the newer ones, but this will add extra costs.

Lastly, this is not perfect, and your printer may not work as well as before so you should make sure that you can afford having your printer out of commission and keep a copy of the firmware for single filament on hand (you will work on it later in this guide) so that you can transition back to the original state to print improved parts or to fix models that may not be working correctly.

**Parts required**

All the following links may be affiliate links (mostly the amazon ones) and I may earn money if a purchase is made using those links. All the profit will go directly back in this project. The price mentioned is only to give you an idea as they may fluctuate. The ones mentioned are the lowest ones I could find including shipping to NA at the date of writing this.

Products in green are the ones that I consider as necessary to buy specifically for this build and in red the ones that you may need to buy but that come in big packs and that you will most likely use for other projects(let’s say that you need only 15 screws for this build and we are not going to count the 700 screws in the pack in the final price) and that you probably already have like M3 bolts and nuts. The red items will be allocated a very small budget but will not be included completely in the final price calculations.
| Part name | Picture | Links | Pcs in pack | Pcs needed | Price $ |
|--|--|--|--|--|--|
| 608 ball bearings| 608 ball bearings |[https://amzn.to/35gdeBc](https://amzn.to/35gdeBc)<br />[https://amzn.to/3olusVk](https://amzn.to/3olusVk)<br />[https://amzn.to/3hQoNny](https://amzn.to/3hQoNny)<br />[https://aliexpi.com/Ep3X](https://aliexpi.com/Ep3X)| 20 <br /> 20 <br /> 10<br /> 10|6|5.17$|
|Heated inserts M3||[https://amzn.to/3pVMIou](https://amzn.to/3pVMIou)<br/> [https://amzn.to/3bfT7qr](https://amzn.to/3bfT7qr) (better choice)|20<br/> 420|4|10$|
|M3 and M2 bolts and nuts| |[https://amzn.to/35dwXSc](https://amzn.to/35dwXSc)|700|≃20|20$|
|PTFE tubing<br/> PC4-M10<br/> PC4-M6||[https://amzn.to/3nBpF0Z](https://amzn.to/3nBpF0Z)<br/>these type of kits include everything you will need and are the best value|4m<br/>8pcs<br/>8pcs|2m<br/>6 pcs<br/>5pcs|10$|
|5mm to 5mm coupler||[https://amzn.to/3otoqSL](https://amzn.to/3otoqSL)<br/>[https://amzn.to/3otoqSL](https://amzn.to/3otoqSL)<br/>if they are available to you I highly recommend going with the non-flexible couplers|2</br>2|1|7$|
|Metal rod 5mmx125mm (a little longer won’t cause any problems)||[https://amzn.to/2Lzjy0b](https://amzn.to/2Lzjy0b)<br/>[https://amzn.to/3nSM61z](https://amzn.to/3nSM61z)|5<br/>10|2|12$|
|MK8 gears with filament groove||[https://amzn.to/3noCCuF](https://amzn.to/3noCCuF)|5|5|8$|
|Nema 17 stepper motor||[https://amzn.to/3osSZbb](https://amzn.to/3osSZbb)|1|1|14$|
|Endstops||[https://amzn.to/3hWqekq](https://amzn.to/3hWqekq)|10|1|8|
|Idler springs|https://i.postimg.cc/RVdy8bJm/image.png|[https://shop.prusa3d.com/en/spare-parts/599-idler-spring.html](https://shop.prusa3d.com/en/spare-parts/599-idler-spring.html) <br/>[https://www.voxelfactory.com/collections/original-prusa-i3-mk2-mk2s-parts/products/replacement-tension-spring-for-prusa-i3-mk2s-or-mk3](https://www.voxelfactory.com/collections/original-prusa-i3-mk2-mk2s-parts/products/replacement-tension-spring-for-prusa-i3-mk2s-or-mk3)|1|2|4-8$|
|total|||||78$|

**Prebuild checks**

Before trying to build this upgrade, you should have a fully working printer, with a compatible mainboard (check below), with Marlin configured properly for a single extruder. You should get the Marlin source code from my GitHub repo: [https://github.com/PierreMasselot1/MMU2-on-any-printer](https://github.com/PierreMasselot1/MMU2-on-any-printer) (I will create a proper fork in the future and create a pull request so that we may have this upgrade in the actual official release of Marlin, but in order to do that I need to be at a more final and stable stage of development). Once you have Marlin configured for your printer before upgrading to the MMU keep a copy in a known location so that you can easily transition back to stock if the upgrade where to fail. After that, download the latest version of PrusaSlicer and follow this guide ([https://www.youtube.com/watch?v=Wz2Soog4HkQ&t=245s](https://www.youtube.com/watch?v=Wz2Soog4HkQ&t=245s) ) on how to set everything up for your printer in a single extruder mode. Once all off that is done download the latest files from my GitHub and start printing them using the methods and settings mentioned below. Check that you also have all the components and tools required.

**Motherboard compatibility**

Your mother board will need to have 5 dedicated stepper motor control (and in case of a dual Z make sure that your printer is using a splitter internally, meaning that you have 6 motor plugs available or use a splitter for your Z axis : [https://amzn.to/35fcFaS](https://amzn.to/35fcFaS) or [https://amzn.to/2L60ard](https://amzn.to/2L60ard) ). Once you have checked that your motherboard supports enough motor controls make sure that you have a way to access to at least two I/O pins: one for the endstop and one for the magnetic rotary encoder (will most likely be an AS5600 in I2C mode) that I am working on. You should also have some access to VCC and ground but even if there are no extra dedicated pins you could easily use one from any of the endstops. You will also need to make sure that you have access to 3.3V (or be ready to convert 5 to 3.3) but as I said your endstops may already have this available. If you have endstop pins for X,Y and Z max you should be good to go.

We are currently working with Paul Lewis to replace/ give the option to have a servo motor controlling the idler instead of a servo motor. This means that we will eventually need only 4 stepper motor control and a servo port (you will need a single free pin and some ways to get your servo connected to vcc and ground).

Mother board with extra endstops connector and easily accessible expansion pins will be the easiest to work with since less tweaking will have to be done to the Pins file of your specific board. If by any chance you were to modify something to fit your setup and think that it could be useful to other people, make sure to let me know and maybe do a pull request.

If your current motherboard isn’t compatible, changing your printer’s mainboard is an easy process and I recommend the SKR 1.4 or SKR PRO V1.1 boards if you are buying them specifically for this

**Printing**

Since we are currently working on the 3d files constantly, you will need to download the original files from GitHub and then convert them into an stl file in order to be able to print them. All the files are currently in .f3d which means that fusion 360 is needed in order to convert them. If you have any problem regarding the stl conversion message me and I will add the STLs in GitHub as well.

**Idler body, pulley body and merger:**

All of those files are in the F3D folder insider the parts folder. In order to convert them to stl you will need to download fusion 360([https://www.autodesk.ca/en/products/fusion-360/personal](https://www.autodesk.ca/en/products/fusion-360/personal) ) after doing all of the setup you will have to open each file, select the object you want to print by right clicking on it and using save as STL



The idler body and the pulley body are both in the same file, the merger and the idler are in a separate file each. Once you have all of them converted to stl they are easy to print, they do not require any support (except the idler but see details below) and you can print them at a 0.2 mm layer height and 0.1mm layer height for the merger. Infill should be at least 20%.

**Idler**

This model prints vertically as shown below:



Once the model is on the build plate you will need to use supports only touching build plate and add a support blocker in the center of the idler.



All of the settings that I am using can easily be found inside other slicers (PrusaSlicer shown below)



once you have selected support blocker you will need to click once at the center of the idler so that no support is printed inside the motor shaft mount. Slice the model using the layer height that you want to use (I personally used 0.2mm)

go into preview mode and use the slider to mark the last layer before closing the bearing enclosure as shown below. In the latest version of the idler there is a step at each end of the bearing to help with friction. You will need to make sure to put the pause before that step.



Use the arrow up and down to go up layer by layer.

Mark down this layer height for each bearing, you should have 5 values for the 5 bearings.

You then have to add a pause at layer line script for each of those values in cura go to extensions-> post processing-> modify gcode->add a script->pause at height.

From the drop-down menu select pause at layer No and change the pause layer to the first value that you took. Repeat with each value.



Reslice your model one last time and start the print, your printer should pause before closing a bearing enclosure and insert the 608 ball bearings before resuming the print.

Once the print is completely done make sure that your bearings can spin freely and insert the heated inserts/embedded nuts into your print (heated inserts position and demo below)



You are now done with the idler.

**For PrusaSlicer**

Use paint on supports to support the endstop slot and support blockers to prevent any supports from blocking the motor shaft.



Layer pause



Right click on the orange plus icon and insert pause print Gcode

Here it is so that you can copy it

G0 X0 Y0

M104 S0 ; standby temperature

M0 ; Do the actual pause

M109 S200 ; resume temperature you may need to change that value to match the material you are using

The merger may require a bit of post processing since any stringing and print defects that happened insider the tube may jam the filament. First try to insert your ptfe tube in each dedicated slot and then put a filament through. If holes themselves seem too tight for the filament you most likely have problems with horizontal expansion, so I recommend that you make use of the help channel on discord. If there seems to be a point where the filament gets jammed then make sure that your ptfe tube is cut straight and properly inserted, if it is the case try to put a bit of pressure on the filament or use a hard object to remove the jam. If there is some slight friction this is normal, and it will get better and better and the merger wears out.

**Assembly:**

Assembly is relatively easy.

The first thing is to assemble the merger and check that it works properly as mentioned previously. It uses only PC4 M10 pneumatic couplers that you should be able to screw in by hand. You may need a bit more force for the end, but it should not take too much force otherwise you could strip the connectors and have to reprint the model.



You can now set the merger aside.



You will then need to setup your motor. Connect the motor and one of the 5mm metal rod. If you are using a flexible coupler, make sure that the two ends are touching to reduce flex to a maximum. Slide all the extruder gears onto the rod but do not tighten them too much yet: the screws used are really small and can be damaged easily and you will need to be further in assembly in order to align the gears properly.



The next parts that will need work are the pulley body and the idler. They both need heated inserts.

[idler picture todo still not reprinted]

If you are not familiar with heated inserts here is a guide: [https://hackaday.com/2019/02/28/threading-3d-printed-parts-how-to-use-heat-set-inserts/](https://hackaday.com/2019/02/28/threading-3d-printed-parts-how-to-use-heat-set-inserts/)

They are not that difficult to use just make sure to not heat up your part for too long.



You can then insert the motor and shaft assembly. Secure the motor using M3*8 screws, if they don’t align with the motor (by about 1mm) checkout the latest update of this model since the previous one didn’t have the correct spacing (with a bit of work even that one worked just not perfectly). You can now align each of the gears with the filament slot corresponding and properly tighten them.



Attach each PC4-M6 couplers to the output of the MMU.



You then have to wire up the endstop for idler body, which you will then secure using M2*12 screws and nuts. It should be facing inward towards the center of the idler



Place a bearing on the end of the idler and pass it through the motor hole of the idler body. You will then be able to press fit it in the dedicated slot.



Once it is done insert the motor in the idler and secure it to the body using M3x8 screws. After this is done put M3x12 screws in the idler (in the heated inserts) and secure it to the motor. No need to tighten them extremely hard since you might rip out the inserts.



After this is done check that the idler can properly rotate and triggers the endstop properly.



Assemble the idler body and pulley body as shown and insert the remaining metal rod through the dedicated holes.



The amount of force required to insert the rods may vary depending on your print settings but I still need feedback regarding clearances so if you have a well calibrated printer let me know whether the clearances are right or whether I need to increase them.



You can now insert the spring and the screws: M3x(from 25 mm up to 35 mm) in order to tension the idler. For now idler tension will be made through trial and error but a good indicator is when you are able to open idler slightly and that the springs push it back in a closed position. I will add visual indicators in a later model as well as find other springs.



You will then need to mount the MMU to your printer. A mount for aluminum extrusions will be designed shortly but you will have to improvise for now, either design your own or use zip ties.

You can then connect the merger to the nozzle. Try to have about 5 cm of space in between so that the filament changes can be as fast as possible but not below 4 cm so that the ptfe tube bend isn’t too hard (potentially causing issues).

You can then connect each of the merger inputs to the MMU outputs making sure that the ptfe tubing is long enough to reach the extremities of the axis.

You are now done with the building process.

**Marlin configuration**

This needs to be done **after** you have successfully configured Marlin for a single extruder setup (You may have seen that in the configuration file there is a default of 3 extruders, but this should not cause any problems when setting up your printer for a single nozzle. If it does you can switch it back to one but remember that you need to switch it back to 3 when configuring for the multi-material upgrade).



This build guide is only for a bowden style setup but as you can see we will soon have support for direct drive. The Bowden tube length will vary depending on your setup but you should try to have it as short as possible since it will directly impact the filament change time



Remember to set your extrude_maxlength higher than your bowden tube length



You should then enable XMAX plug (uncomment it by removing the //) since this is what we are going to be using to home the idler. If you board does not have an XMAX endstop you can find a free IO pin and connect your enstop to that, but you will need to configure an XMAX enstop inside your boards pins file similarly to what is shown below. If you need help with that step reach out to me on the discord server.


You may also need to invert the endstop logic depending on your board. If the idler doesn’t home (considers the endstop as always triggered) this may be the problem. Usually this will be like your other endstops.



You will also need to define driver type for each motor



Similarly to your XYZ axis you can change the direction of the extruder stepper in order to match the expected behavior. If when homing the idler goes in the opposite direction you would change E1 dir to false(Or E x if you have setup custom extruder pins)

You are now done with the software modifications.

**Slicer settings.**

You will now need to configure the slicer in order to adapt it to your printer.

You can use the same slicer profile that you were using or create a new one (recommended)

The first thing you will need to do is change the number of extruders to 3, in the printer settings tab and to check the single extruder multi material



You also need to use relative E distance

You should now have 5 extruders to work with.

In there you can change retraction settings (choose a setting similar to what you were using before) and also select the extruder color: extremely useful for multi-color prints.



Now go to the single extruder multimaterial parameters(Single extruder MM setup)

You will have four things to adjust. First off, the cooling tube position. In order to find it simply measure from your nozzle to the middle of the cooling block on your extruder. The cooling tube length will vary depending on your extruder but 10mm seems to be a good value for most extruders. The filament parking position should be the cooling tube position+ (the cooling tube length/2) since we are handling the unloading and reloading in Marlin (may not be as necessary right now but when working with less capable boards will enable us to make some really interesting stuff…  more info on that later) the extra loading distance should be at 0 and be tweaked if you find that it doesn’t start extruding exactly when restarting (this is irrelevant when using a wipe tower).



You will then go in filament settings and make sure that you have keep fan always on turned on since it will stop when doing tool changes and not turn on for small patch of color.



Then go in advanced and change 4 things. The number of cooling moves: too low and it will jam and too high and it will take a huge amount of time. 3 seems to work well for me, the speed of the cooling move can also be adjusted but it doesn’t matter much, a little faster will speed up a filament change



In here you can adjust the filament change time in order to get more accurate time extimates for your print. While the speed is constantly changing as I improve the loading and unloading sequence and since it will also vary based on your ptfe tube length I recommend you measure the tool change time for your setup by sending T1 or any toolchange gcode and measure the time that it takes. This setting is very usefull since leaving it at 0 will give you some extremly optimistic results and on a 15 hr print it may be off by up to two hour, and this can result in lack of sleep...don't ask me why.
The last thing in there that your will need to adjust is the ramming setting. The default one seems to work but with a bit of tweaking you can get a way cleaner filament tip the following picture is an example of what I am running but you will need to do a bit of experimenting on your side.



You just need to click on ramming settings to get access to these controls.

In print settings make sure that you have the wipe tower enabled inside of the Multiple extruder tab and prime all printing extruders enabled as well.



You are now done with slicer settings.

To print you will just need to import a multicolor model. Launch prusa slicer, open all the parts of your model at the same time.



Click open



Hit yes

You will then be able to select different extruders on the right hand side of your screen. Happy printing!

If you have any problems, make sure to message me on discord so that I can both help you and improve the documentation.

**Tips to get a successful multicolor print.**

Idler tension is key to get good prints. If you see any extrusion discrepancies or under extrusion, then the fix will most likely be to increase idler tension.

If your filaments are all new, then it is recommended to turn on prime all printing extruders since it will shape all the filaments at the start of the print which will help you detect any problems at the beginning.

Another failure point that I have seen is on the coupler and the gears, if they are not tight enough, they will slip on the rod, resulting in under extrusion or even no extrusion in some cases.

The purge block is a huge waste of filament, but it can be adjusted based on the filament transition (transitioning from blue to cyan will require less purging that from black to white). Other things like wipe in object and wipe in infill can be enabled an optimized in order to reduce filament waste.

**Working on**

As I said this not a final version and I am working on multiple improvements. First off, use interface on the lcd to be easily able to load in new filaments, select a specific filament when working with a single extruder print.

I am also working on a filament sensor which would help a lot with filament load failures, filament jams, filament slipping in the extruder and would help a lot with the success rate of multicolor and single-color prints.

Servomotor controlled idler: no need for homing, more board compatibility since no stepper drivers required

A lot of nice to have features and complex multi-material 3d designs to demonstrate the capabilities of such multi-material upgrades, using different materials as well as some that are not supposed to bond well together (I have a few ideas of 3d printing processes that could fix that).

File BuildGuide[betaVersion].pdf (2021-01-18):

Multi-material upgrade on any printer: BUILD GUIDE

The aim of this project is to popularize multi-material 3d printing by making a more reliable, cheaper, and hopefully better multi-material upgrade based on the MMU2 from Prusa. There is still a lot of work to do but this is prototype that works well enough to be considered as viable. Before you attempt to build this:

This guide is currently meant for more advanced user, comfortable with Marlin configuration and with a bit of programming experience. The models may still need work and are not final. You will need to do a lot of tuning before you get everything going, parts modification may be required, and you will almost certainly need to do some troubleshooting. If you think this is too much for you do not worry, I will be releasing a tutorial that goes way more in depth and should be easier to follow, the models shown and provided in this video will be tested on multiple printers and the risk of something not working will be reduced by a lot. If you are still reading this and want to build this for yourself, I highly recommend you join the discord server. There is a help channel in there specifically to answer any questions or issues you have while building the MMU.

There are also a few things to know before deciding to build this upgrade. I don’t take any responsibility regarding your actions, this is still a prototype and requires heavy modifications of your printer, which could result in permanent damage, which is a risk that you should be willing to take if attempting this build.

There will also be improvements that may require extra parts in the future, you should be easily able to transition from this version to the newer ones, but this will add extra costs.

Lastly, this is not perfect, and your printer may not work as well as before so you should make sure that you can afford having your printer out of commission and keep a copy of the firmware for single filament on hand (you will work on it later in this guide) so that you can transition back to the original state to print improved parts or to fix models that may not be working correctly. Parts required

All the following links may be affiliate links (mostly the amazon ones) and I may earn money if a purchase is made using those links. All the profit will go directly back in this project. The price mentioned is only to give you an idea as they may fluctuate. The ones mentioned are the lowest ones I could find including shipping to NA at the date of writing this.

Products in green are the ones that I consider as necessary to buy specifically for this build and in red the ones that you may need to buy but that come in big packs and that you will most likely use for other projects(let’s say that you need only 15 screws for this build and we are not going to count the 700 screws in the pack in the final price) and that you probably already have like M3 bolts and nuts. The red items will be allocated a very small budget but will not be included completely in the final price calculations.

Part name | Picture | Links | Pcs in pac k | Pcs neede d | Pric e $
608 ball bearings | | https://amzn.to/35gdeBchttps://amzn.to/3olusVkhttps://amzn.to/3hQoNnyhttps://aliexpi.com/Ep3X | 20 20 10 10 | 6 | 5.17 $
Heated inserts M3 | | https://amzn.to/3pVMIouhttps://amzn.to/3bfT7qr (better choice) | 20 420 | 4 | 10$
M3 and M2 bolts and nuts | | https://amzn.to/35dwXSc | 700 | ≃20 | 20$
PTFE tubing PC4-M10 PC4-M6 | | https://amzn.to/3nBpF0Z these type of kits include everything you will need and are the best value | 4m 8 pcs 8 pcs | 2m 6 pcs 5pcs | 10$
5mm to 5mm coupler | | https://amzn.to/35pzHf7https://amzn.to/3otoqSL if they are available to you I highly recommend going with the non-flexible couplers | 2 2 | 1 | 7$
Metal rod 5mmx125m m (a little longer won’t cause any problems) | | https://amzn.to/2Lzjy0bhttps://amzn.to/3nSM61z | 5 2 | 2 2 | 12$
MK8 gears with filament groove | | https://amzn.to/3noCCuF | 5 | 5 | 8$

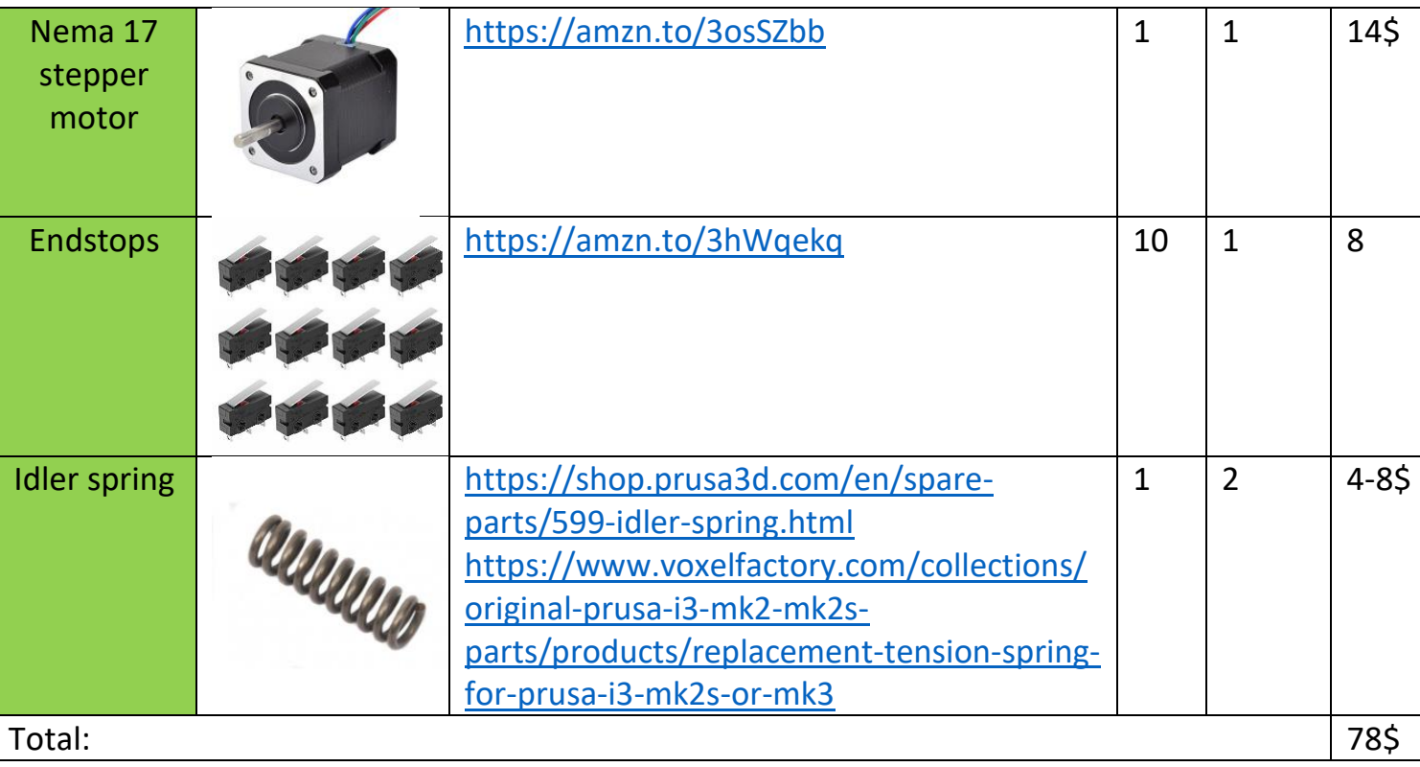
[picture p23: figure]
Nema 17 stepper motor; https://amzn.to/3osSZbb; Endstops; https://amzn.to/3hWqekq; Idler spring; https://shop.prusa3d.com/en/spare-parts/599-idler-spring.html (https://shop.prusa3d.com/en/spare-parts/599-idler-spring.html) https://www.voxelfactory.com/collections/original-prusa-i3-mk2-mk2s-parts/products/replacement-tension-spring-for-prusa-i3-mk2s-or-mk3 (https://www.voxelfactory.com/collections/original-prusa-i3-mk2-mk2s-parts/products/replacement-tension-spring-for-prusa-i3-mk2s-or-mk3); Total:

Prebuild checks

Before trying to build this upgrade, you should have a fully working printer, with a compatible mainboard (check below), with Marlin configured properly for a single extruder. You should get the Marlin source code from my GitHub repo: https://github.com/PierreMasselot1/MMU2-on-any-printer (https://github.com/PierreMasselot1/MMU2-on-any-printer) (I will create a proper fork in the future and create a pull request so that we may have this upgrade in the actual official release of Marlin, but in order to do that I need to be at a more final and stable stage of development). Once you have Marlin configured for your printer before upgrading to the MMU keep a copy in a known location so that you can easily transition back to stock if the upgrade where to fail. After that, download the latest version of PrusaSlicer and follow this guide (https://www.youtube.com/watch?v=Wz2Soog4HkQ&t=245s ) on how to set everything up for your printer in a single extruder mode. Once all off that is done download the latest files from my GitHub and start printing them using the methods and settings mentioned below. Check that you also have all the components and tools required.

Motherboard compatibility

Your mother board will need to have 5 dedicated stepper motor control (and in case of a dual Z make sure that your printer is using a splitter internally, meaning that you have 6 motor plugs available or use a splitter for your Z axis : https://amzn.to/35fcFaS or https://amzn.to/2L60ard ).

Once you have checked that your motherboard supports enough motor controls make sure that you have a way to access to at least two I/O pins: one for the endstop and one for the magnetic rotary encoder (will most likely be an AS5600 in I2C mode) that I am working on. You should also have some access to VCC and ground but even if there are no extra dedicated pins you could easily use one from any of the endstops. You will also need to make sure that you have access to 3.3V (or be ready to convert 5 to 3.3) but as I said your endstops may already have this available. If you have endstop pins for X,Y and Z max you should be good to go.

We are currently working with Paul Lewis to replace/ give the option to have a servo motor controlling the idler instead of a servo motor. This means that we will eventually need only 4 stepper motor control and a servo port (you will need a single free pin and some ways to get your servo connected to vcc and ground).

Mother board with extra endstops connector and easily accessible expansion pins will be the easiest to work with since less tweaking will have to be done to the Pins file of your specific board. If by any chance you were to modify something to fit your setup and think that it could be useful to other people, make sure to let me know and maybe do a pull request.

If your current motherboard isn’t compatible, changing your printer’s mainboard is an easy process and I recommend the SKR 1.4 or SKR PRO V1.1 boards if you are buying them specifically for this
Printing

Since we are currently working on the 3d files constantly, you will need to download the original files from GitHub and then convert them into an stl file in order to be able to print them. All the files are currently in .f3d which means that fusion 360 is needed in order to convert them. If you have any problem regarding the stl conversion message me and I will add the STLs in GitHub as well.

Idler body, pulley body and merger:

All of those files are in the F3D folder insider the parts folder. In order to convert them to stl you will need to download fusion 360(https://www.autodesk.ca/en/products/fusion-360/personal ) after doing all of the setup you will have to open each file, select the object you want to print by right clicking on it and using save as STL

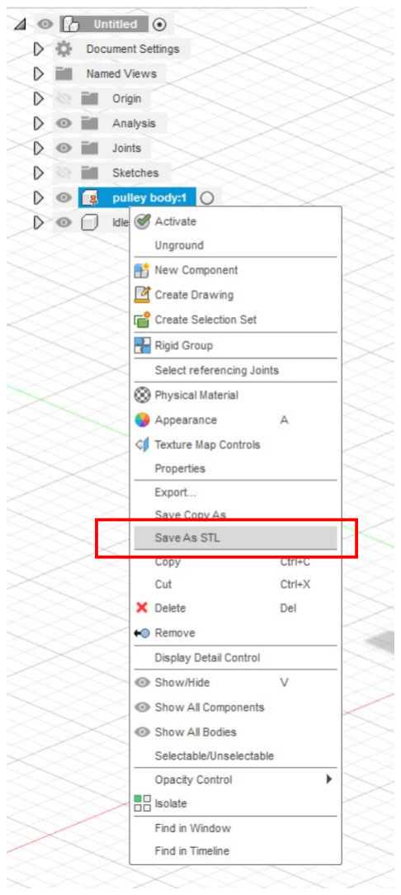
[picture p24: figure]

The idler body and the pulley body are both in the same file, the merger and the idler are in a separate file each. Once you have all of them converted to stl they are easy to print, they do not require any support (except the idler but see details below) and you can print them at a 0.2 mm layer height and 0.1mm layer height for the merger. Infill should be at least 20%.

Idler

This model prints vertically as shown below:

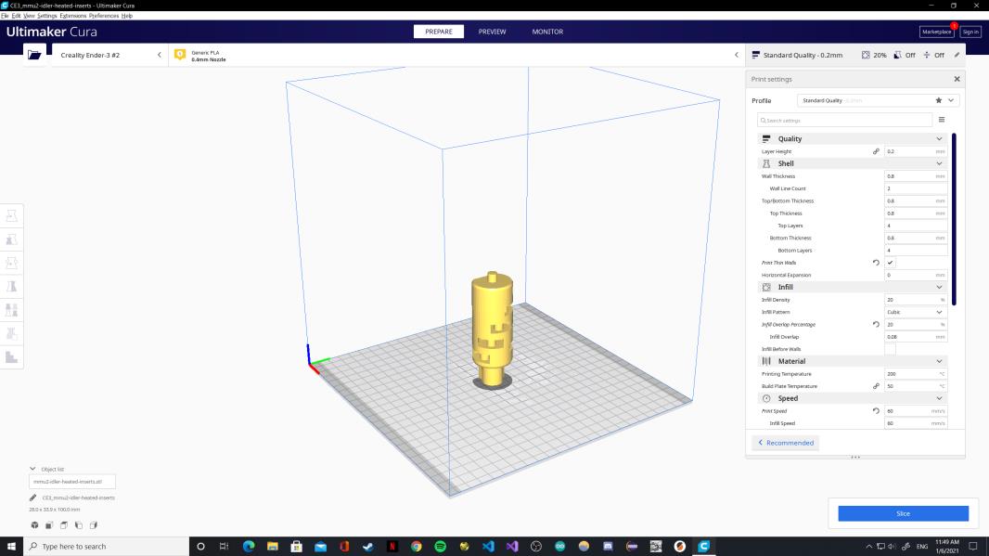
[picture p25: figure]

Once the model is on the build plate you will need to use supports only touching build plate and add a support blocker in the center of the idler.

All of the settings that I am using can easily be found inside other slicers (PrusaSlicer shown below)

once you have selected support blocker you will need to click once at the center of the idler so that no support is printed inside the motor shaft mount. Slice the model using the layer height that you want to use (I personally used 0.2mm)

go into preview mode and use the slider to mark the last layer before closing the bearing enclosure as shown below

Use the arrow up and down to go up layer by layer.

Mark down this layer height for each bearing, you should have 5 values for the 5 bearings.

You then have to add a pause at layer line script for each of those values in cura go to extensions-> post processing-> modify gcode->add a script->pause at height.

From the drop-down menu select pause at layer No and change the pause layer to the first value that you took. Repeat with each value.

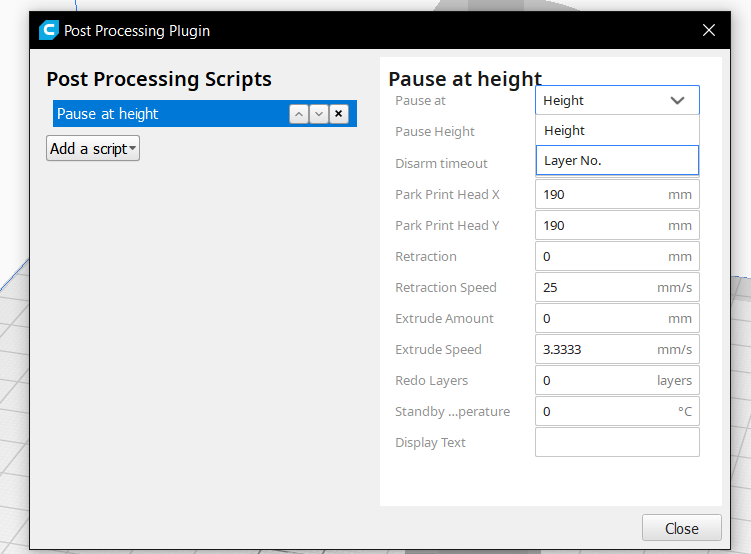
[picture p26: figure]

Reslice your model one last time and start the print, your printer should pause before closing a bearing enclosure and insert the 608 ball bearings before resuming the print.

Once the print is completely done make sure that your bearings can spin freely and insert the heated inserts/embedded nuts into your print (heated inserts position and demo below)

You are now done with the idler.

For PrusaSlicer

Use paint on supports to support the endstop slot and support blockers to prevent any supports from blocking the motor shaft.

Layer pause

Right click on the orange plus icon and insert pause print Gcode

Here it is so that you can copy it

M83 ; switch to relative E values for any needed retraction

G1 F300 Z1.4 ; move up a millimeter to get out of the way

G1 F9000 X190 Y190

G1 F300 Z15 ; too close to bed--move to at least 15mm

M104 S0 ; standby temperature

M0 ; Do the actual pause

M109 S200 ; resume temperature

G1 F300 Z1.4

G1 F9000 X112.202 Y142.569

G1 F300 Z0.4 ; move back down to resume height

G1 F1200 ; restore extrusion feedrate

M82 ; switch back to absolute E values

G92 E241.49746

The merger may require a bit of post processing since any stringing and print defects that happened insider the tube may jam the filament. First try to insert your ptfe tube in each dedicated slot and then put a filament through. If holes themselves seem too tight for the filament you most likely have problems with horizontal expansion, so I recommend that you make use of the help channel on discord. If there seems to be a point where the filament gets jammed then make sure that your ptfe tube is cut straight and properly inserted, if it is the case try to put a bit of pressure on the filament or use a hard object to remove the jam. If there is some slight friction this is normal, and it will get better and better and the merger wears out.

Assembly:

Assembly is relatively easy.

The first thing is to assemble the merger and check that it works properly as mentioned previously. It uses only PC4 M10 pneumatic couplers that you should be able to screw in by hand. You may need a bit more force for the end, but it should not take too much force otherwise you could strip the connectors and have to reprint the model.

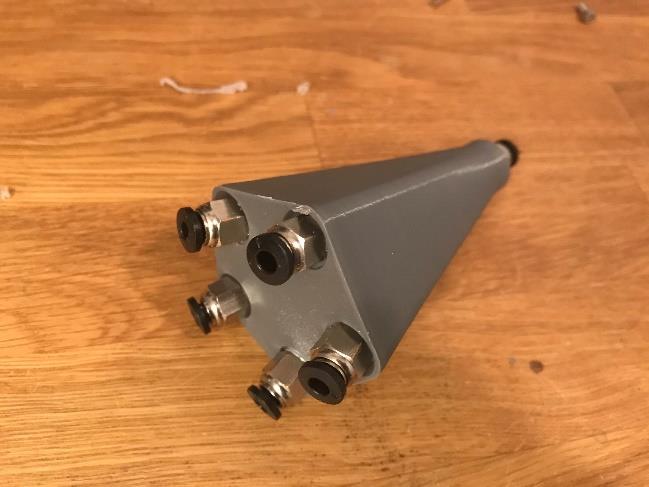
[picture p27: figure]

You can now set the merger aside.

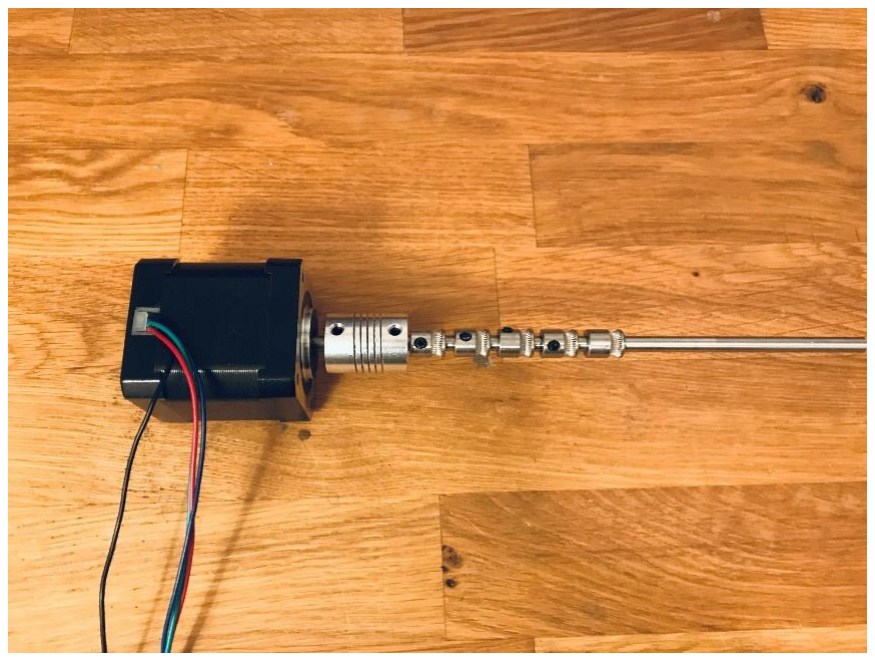
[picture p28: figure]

You will then need to setup your motor. Connect the motor and one of the 5mm metal rod. If you are using a flexible coupler, make sure that the two ends are touching to reduce flex to a maximum. Slide all the extruder gears onto the rod but do not tighten them too much yet: the screws used are really small and can be damaged easily and you will need to be further in assembly in order to align the gears properly.

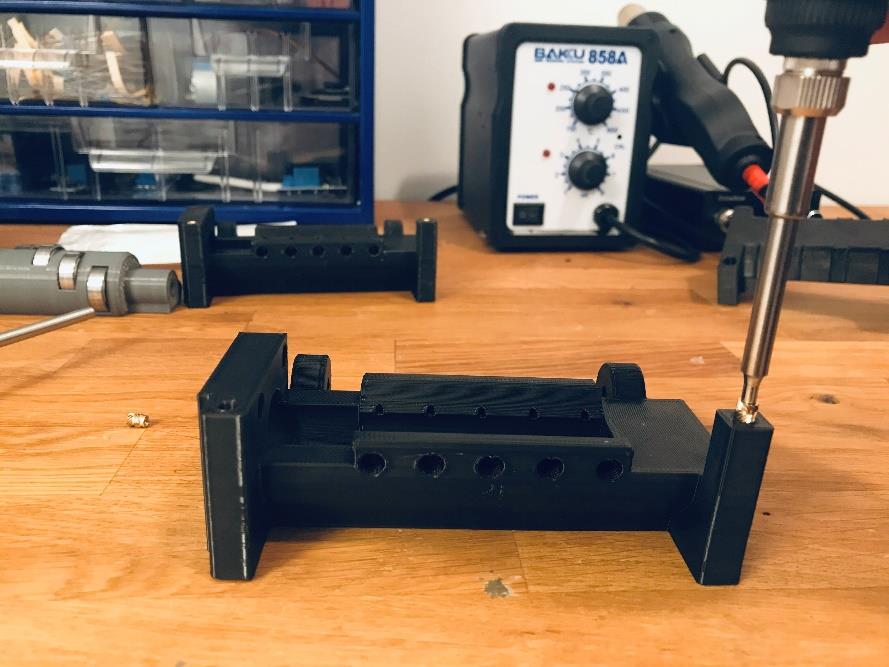
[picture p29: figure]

The next parts that will need work are the pulley body and the idler. They both need heated inserts.

[idler picture todo still not reprinted]

If you are not familiar with heated inserts here is a guide: https://hackaday.com/2019/02/28/threading-3d-printed-parts-how-to-use-heat-set-inserts/

They are not that difficult to use just make sure to not heat up your part for too long.

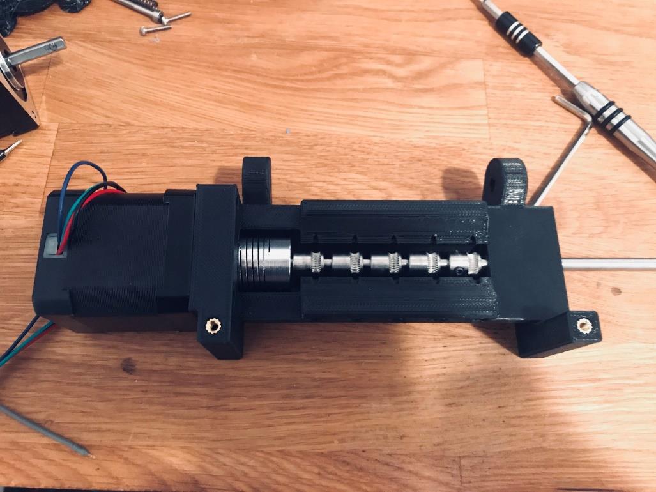
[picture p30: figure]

You can then insert the motor and shaft assembly. Secure the motor using M3*8 screws, if they don’t align with the motor (by about 1mm) checkout the latest update of this model since the previous one didn’t have the correct spacing (with a bit of work even that one worked just not perfectly). You can now align each of the gears with the filament slot corresponding and properly tighten them.

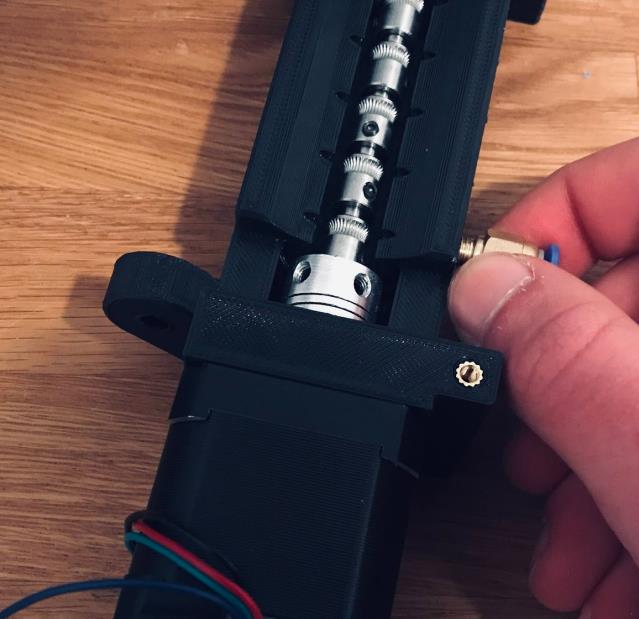
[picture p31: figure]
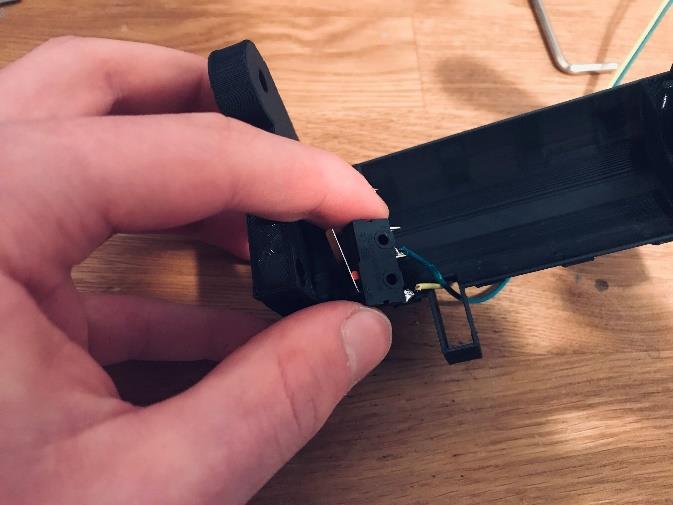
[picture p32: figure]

Attach each PC4-M6 couplers to the output of the MMU.

You then have to wire up the endstop for idler body, which you will then secure using M2*12 screws and nuts. It should be facing inward towards the center of the idler

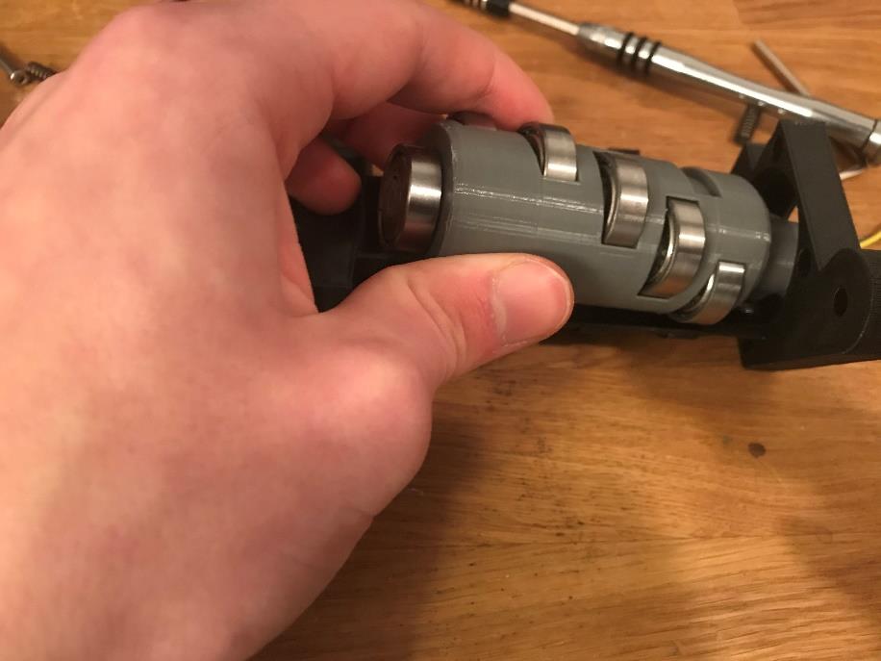
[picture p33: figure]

Place a bearing on the end of the idler and pass it through the motor hole of the idler body. You will then be able to press fit it in the dedicated slot.

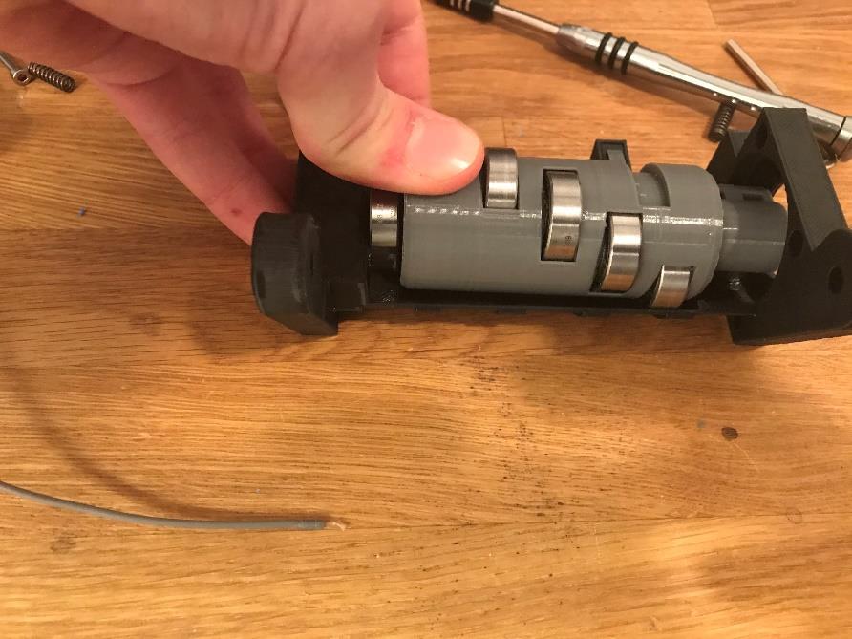
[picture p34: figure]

Once it is done insert the motor in the idler and secure it to the body using M3x8 screws. After this is done put M3x12 screws in the idler (in the heated inserts) and secure it to the motor. No need to tighten them extremely hard since you might rip out the inserts.

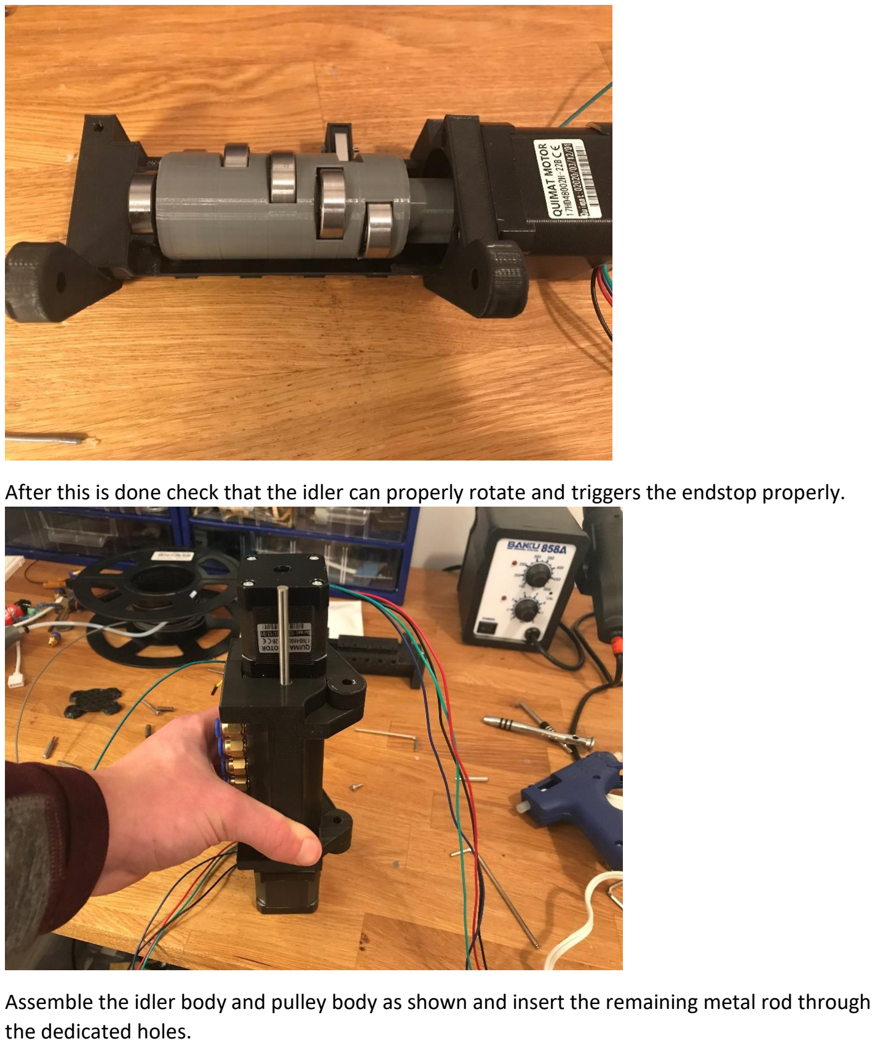
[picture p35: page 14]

After this is done check that the idler can properly rotate and triggers the endstop properly.

Assemble the idler body and pulley body as shown and insert the remaining metal rod through the dedicated holes.

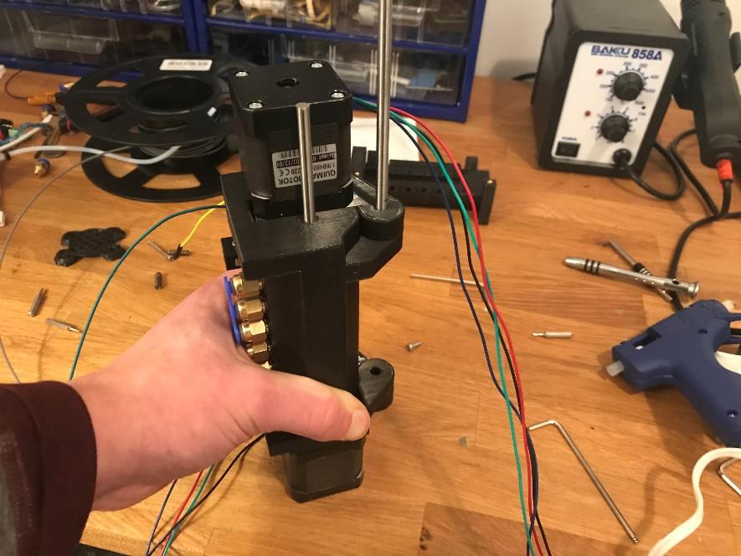
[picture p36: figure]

The amount of force required to insert the rods may vary depending on your print settings but I still need feedback regarding clearances so if you have a well calibrated printer let me know whether the clearances are right or whether I need to increase them.

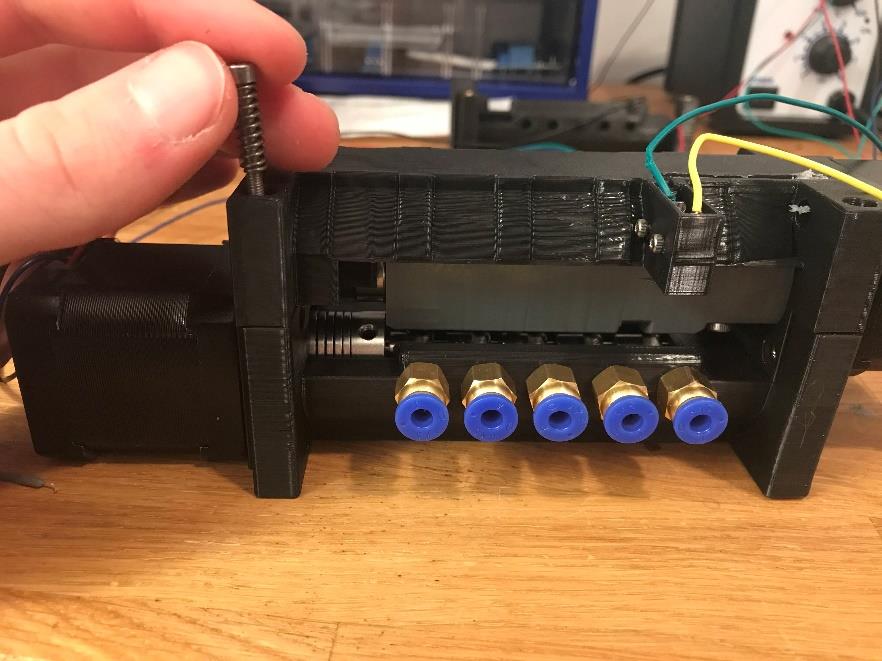
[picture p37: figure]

You can now insert the spring and the screws: M3x(from 25 mm up to 35 mm) in order to tension the idler. For now idler tension will be made through trial and error but a good indicator is when you are able to open idler slightly and that the springs push it back in a closed position. I will add visual indicators in a later model as well as find other springs.

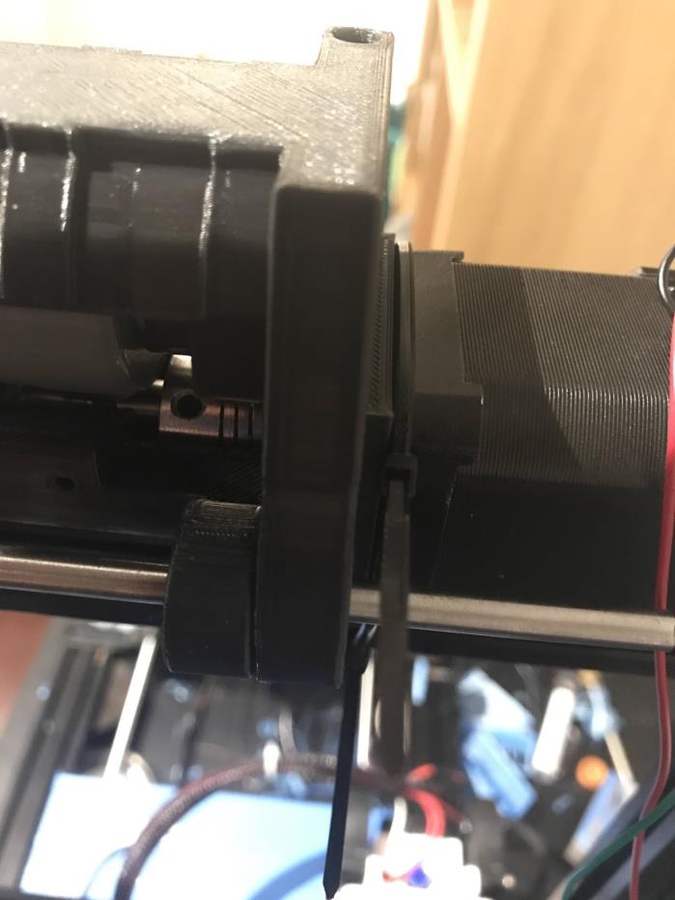
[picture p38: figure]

You will then need to mount the MMU to your printer. A mount for aluminum extrusions will be designed shortly but you will have to improvise for now, either design your own or use zip ties.

You can then connect the merger to the nozzle. Try to have about 5 cm of space in between so that the filament changes can be as fast as possible but not below 4 cm so that the ptfe tube bend isn’t too hard (potentially causing issues).

You can then connect each of the merger inputs to the MMU outputs making sure that the ptfe tubing is long enough to reach the extremities of the axis.

You are now done with the building process.

Marlin configuration

This needs to be done after you have successfully configured Marlin for a single extruder setup (You may have seen that in the configuration file there is a default of 3 extruders, but this should not cause any problems when setting up your printer for a single nozzle. If it does you can switch it back to one but remember that you need to switch it back to 3 when configuring for the multimaterial upgrade).

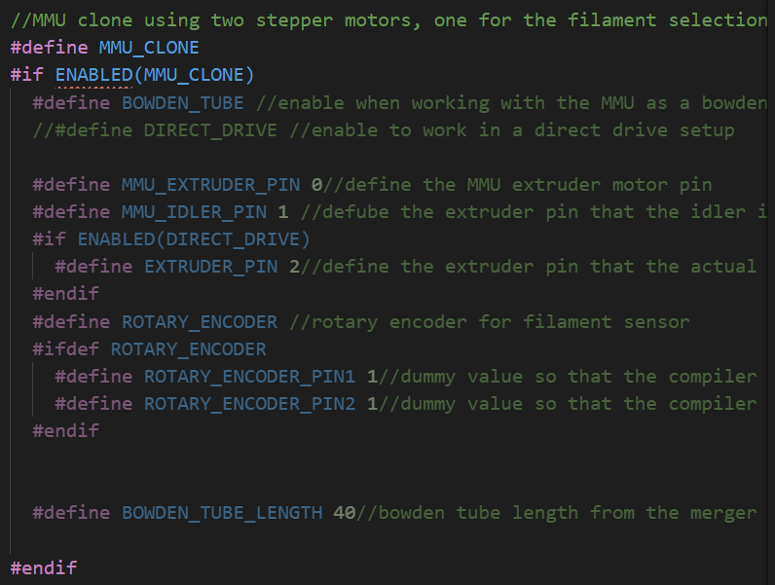
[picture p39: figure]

This build guide is only for a bowden style setup but as you can see we will soon have support for direct drive. The Bowden tube length will vary depending on your setup but you should try to have it as short as possible since it will directly impact the filament change time

Remember to set your extrude_maxlength higher than your bowden tube length

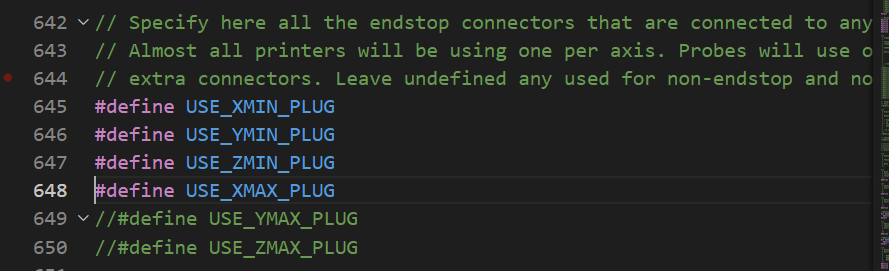
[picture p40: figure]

You should then enable XMAX plug (uncomment it by removing the //) since this is what we are going to be using to home the idler. If you board does not have an XMAX endstop you can find a free IO pin and connect your enstop to that, but you will need to configure an XMAX enstop inside your boards pins file similarly to what is shown below. If you need help with that step reach out to me on the discord server.

You may also need to invert the endstop logic depending on your board. If the idler doesn’t home (considers the endstop as always triggered) this may be the problem. Usually this will be like your other endstops.

You will also need to define driver type for each motor

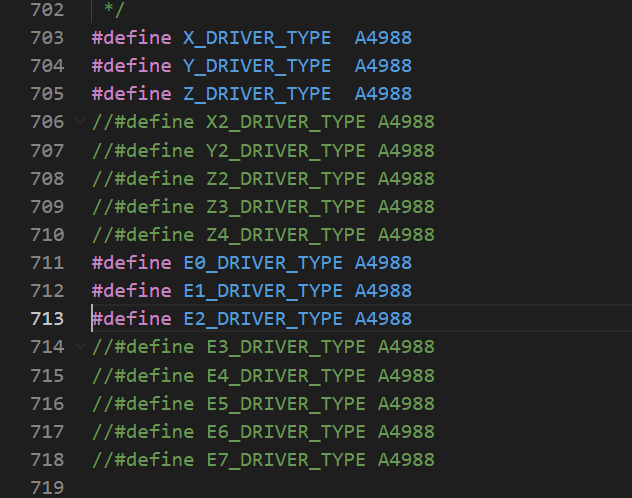
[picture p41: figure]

Similarly to your XYZ axis you can change the direction of the extruder stepper in order to match the expected behavior. If when homing the idler goes in the opposite direction you would change E1 dir to false(Or E x if you have setup custom extruder pins)

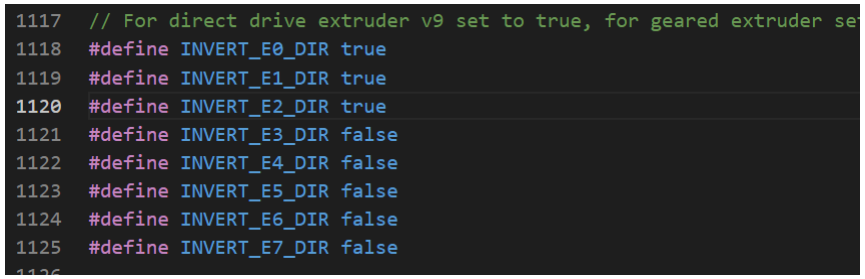
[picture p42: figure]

You are now done with the software modifications.

Slicer settings.

You will now need to configure the slicer in order to adapt it to your printer.

You can use the same slicer profile that you were using or create a new one (recommended)

The first thing you will need to do is change the number of extruders to 3, in the printer settings tab and to check the single extruder multi material

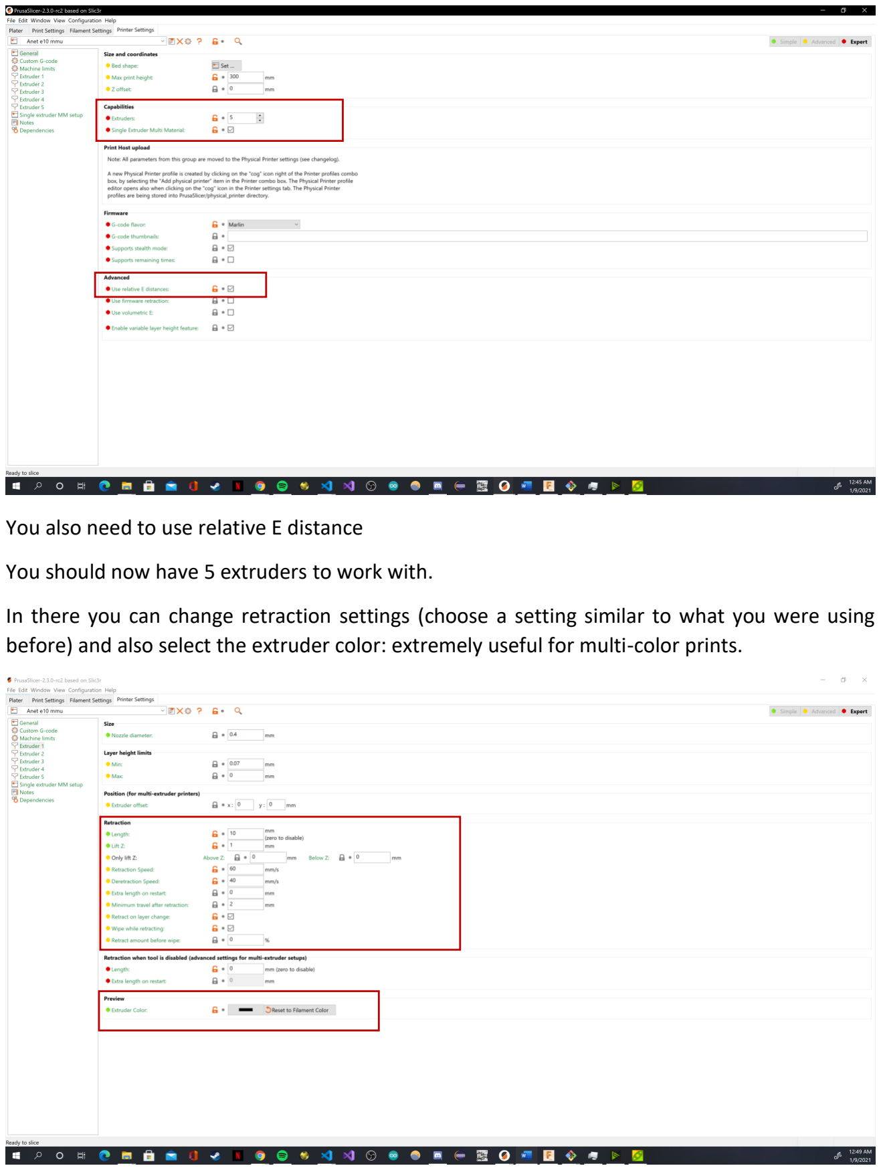
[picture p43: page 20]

You also need to use relative E distance

You should now have 5 extruders to work with.

In there you can change retraction settings (choose a setting similar to what you were using before) and also select the extruder color: extremely useful for multi-color prints.

Now go to the single extruder multimaterial parameters(Single extruder MM setup)

You will have four things to adjust. First off, the cooling tube position. In order to find it simply measure from your nozzle to the middle of the cooling block on your extruder. The cooling tube length will vary depending on your extruder but 10mm seems to be a good value for most extruders. The filament parking position should be the cooling tube position+ (the cooling tube length/2) since we are handling the unloading and reloading in Marlin (may not be as necessary right now but when working with less capable boards will enable us to make some really interesting stuff… more info on that later) the extra loading distance should be at 0 and be tweaked if you find that it doesn’t start extruding exactly when restarting (this is irrelevant when using a wipe tower).

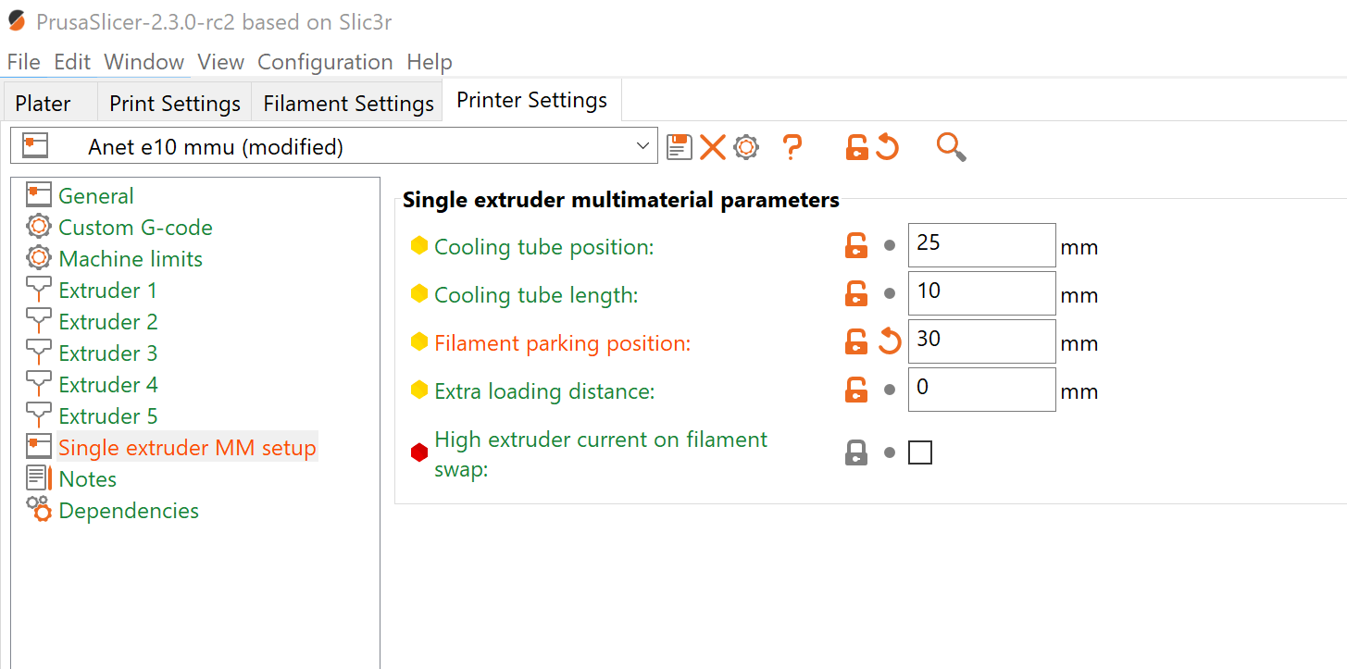
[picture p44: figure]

You will then go in filament settings and make sure that you have keep fan always on turned on since it will stop when doing tool changes and not turn on for small patch of color.

Then go in advanced and change 4 things. The number of cooling moves: too low and it will jam and too high and it will take a huge amount of time. 3 seems to work well for me, the speed of the cooling move can also be adjusted but it doesn’t matter much, a little faster will speed up a filament change

The last thing in there that your will need to adjust is the ramming setting. The default one seems to work but with a bit of tweaking you can get a way cleaner filament tip the following picture is an example of what I am running but you will need to do a bit of experimenting on your side.

You just need to click on ramming settings to get access to these controls.

In print settings make sure that you have the wipe tower enabled inside of the Multiple extruder tab and prime all printing extruders enabled as well.

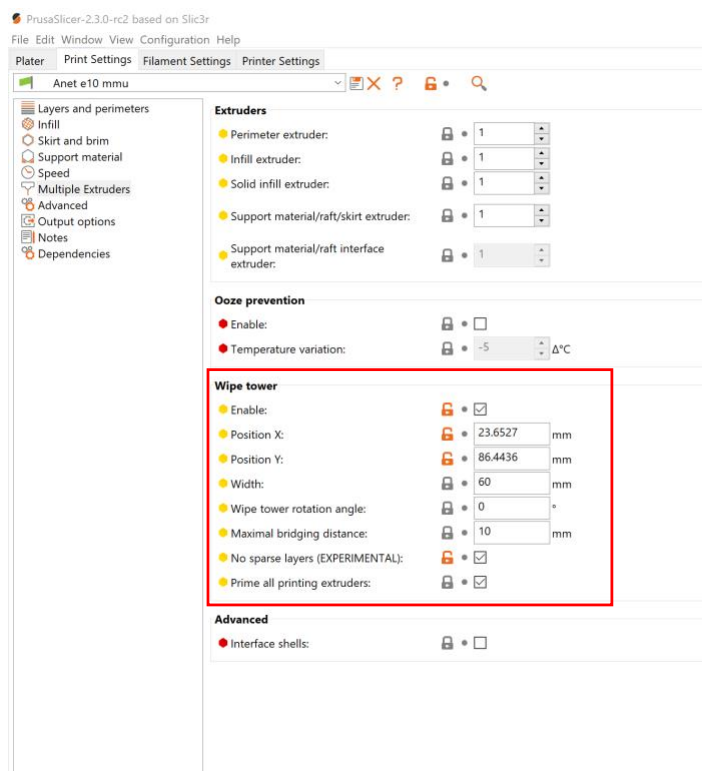
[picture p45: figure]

You are now done with slicer settings.

To print you will just need to import a multicolor model. Launch prusa slicer, open all the parts of your model at the same time.

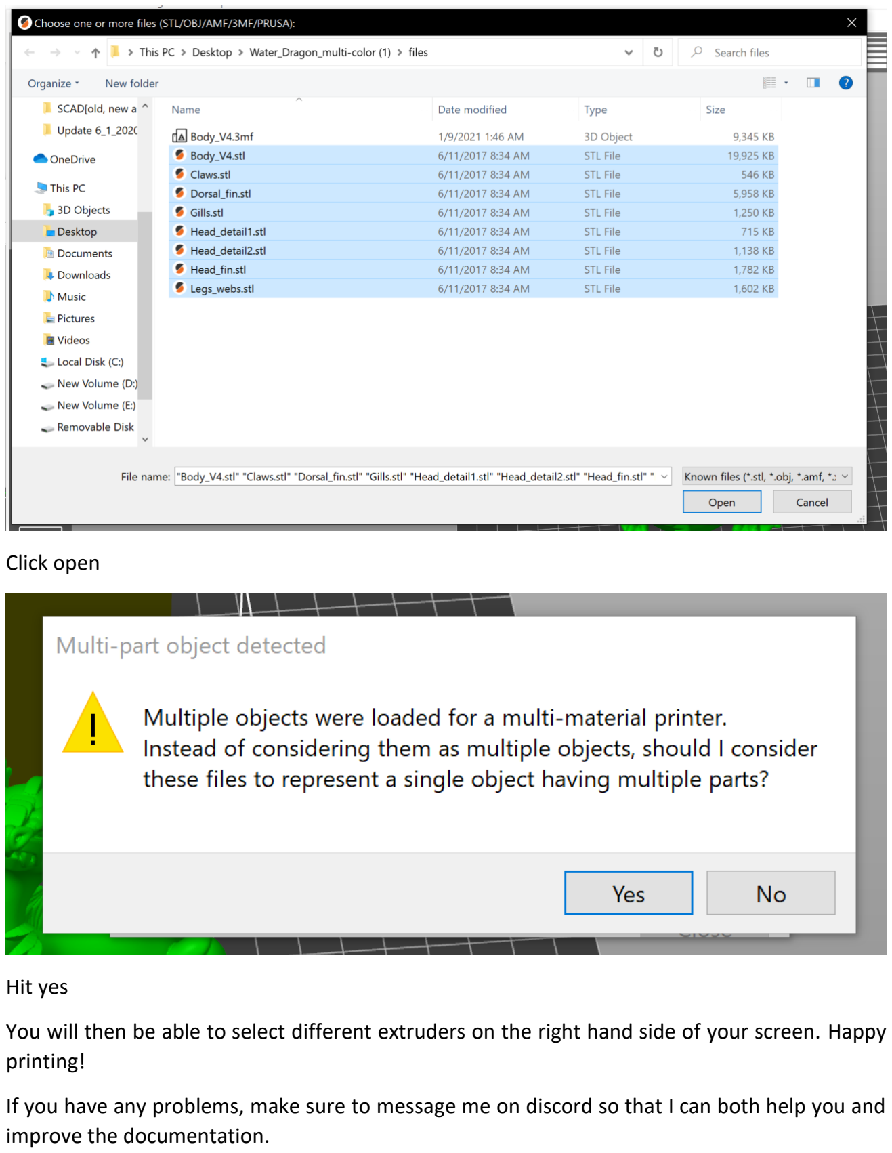
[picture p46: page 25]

Click open

Hit yes

You will then be able to select different extruders on the right hand side of your screen. Happy printing!

If you have any problems, make sure to message me on discord so that I can both help you and improve the documentation.

Tips to get a successful multicolor print.

Idler tension is key to get good prints. If you see any extrusion discrepancies or under extrusion, then the fix will most likely be to increase idler tension.

If your filaments are all new, then it is recommended to turn on prime all printing extruders since it will shape all the filaments at the start of the print which will help you detect any problems at the beginning.

Another failure point that I have seen is on the coupler and the gears, if they are not tight enough, they will slip on the rod, resulting in under extrusion or even no extrusion in some cases.

The purge block is a huge waste of filament, but it can be adjusted based on the filament transition (transitioning from blue to cyan will require less purging that from black to white). Other things like wipe in object and wipe in infill can be enabled an optimized in order to reduce filament waste.

Working on

As I said this not a final version and I am working on multiple improvements. First off, use interface on the lcd to be easily able to load in new filaments, select a specific filament when working with a single extruder print.

I am also working on a filament sensor which would help a lot with filament load failures, filament jams, filament slipping in the extruder and would help a lot with the success rate of multicolor and single-color prints.

Servomotor controlled idler: no need for homing, more board compatibility since no stepper drivers required

A lot of nice to have features and complex multi-material 3d designs to demonstrate the capabilities of such multi-material upgrades, using different materials as well as some that are not supposed to bond well together (I have a few ideas of 3d printing processes that could fix that).

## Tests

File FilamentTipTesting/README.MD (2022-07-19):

This is a small python script meant to isolate a tool change inside a gcode file in order to easily test the filament ramming and cooling settings
This means that in order to test those slice settings you can now slice the models provided (or any model for that matter, having a small gcode file just helps with the processing time) using two different extruders and save the gcode file as test.gcode (replacing the file that is currently in this folder) you can then run the python script which will overwrite the second file TipTest.gcode. You can then load that file(TipTest.gcode) on your sd card and run it on your printer. When running it the printer should heat up to the chosen temperature and perform a small extrusion then perform the ramming and cooling sequence, followed by a quick retraction to keep the filament far from the melt-zone and keep the tip as is.

# Optional 

To get the filament profile name to work, add the upper circled text in your slicer's filament profile custom gcode field followed exactly 4 lines below by the lower circled text.  The trigger text and line offset (4 in this case) is contained in the python script in lines 20 and 21 if they need to be changed/adjusted for your setup.

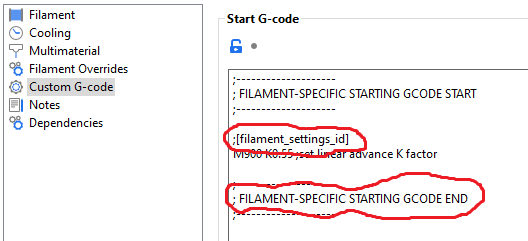
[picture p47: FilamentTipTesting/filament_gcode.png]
Gcode settings image


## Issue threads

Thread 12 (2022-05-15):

SuperSlicer, wait for temp before continuing the print after a tool change with cooldown before extraction

PierreMasselot1, 2022-05-15:

PierreMasselot1, 2022-09-10:
In progress, currently in https://github.com/PierreMasselot1/SuperSlicer/commit/17a63c612225ecda020a5dcd9d5d422a8fea66a3

PierreMasselot1, 2022-09-16:
Done, just needs to be merged into super slicer

Closed 2022-09-16.

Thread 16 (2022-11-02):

Create lighter merger

PierreMasselot1, 2022-11-02:

PierreMasselot1, 2024-05-23:
https://www.printables.com/model/751314-bowden-2-3-5-way-splitters

currently testing this coupler-less solution and it seems to be a really good lightweight alternative. Just need to check for reliability on long use and maybe modify the model a bit.

PierreMasselot1, 2024-06-09:
it is reliable but not super happy with how much variance there is based on what type of PTFE tubing you use). Also, too much tweaking is required (if you go too far the tubing gets compressed inside the taper).

Closed 2024-06-09.

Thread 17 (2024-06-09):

Tweak clearances on the idler bearing press fit

PierreMasselot1, 2024-06-09:

Closed 2024-06-09.

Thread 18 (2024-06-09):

Create new merger

PierreMasselot1, 2024-06-09:
- needs to be relatively light (no full-size PC connectors)
- part calibration with 5 or 6 different clearance options (horizontal hole compensation, filament expansion, and other factors mean that getting an accurate filament path is extremely set up dependent)
- focus on reliability for this first version (high retractions might be needed because of a looser filament path but can be solved down the line)

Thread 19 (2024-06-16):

selecting an already active extruder

rozhkovets, 2024-06-16:
If you send a command to select an already active extruder, then unloading and loading occurs. This is a useless action. Additional verification needs to be added.

Example:
When you turn on the printer for the first time, the active extruder is set to T0.
In the slicer, the T0 selection command is automatically added to the beginning of the g-code.
At the beginning of printing we get a useless action.

```
void MSUMP::tool_change(uint8_t index)
{
  if (index != active_extruder) {
  ...
  }
}
```

rozhkovets, 2024-07-01:
I haven't tested it, but it seems to me that the first call to T0 after loading will cause a useless tool change because.
```
float selected_filament_nbr = -1;
...
void MSUMP::tool_change(uint8_t index) {

 // Check if a toolcahnge is necessary
 if (selected_filament_nbr == index)
```

rozhkovets, 2024-07-03:
I also noticed this. I'll try to describe it step by step.
1)turn on the printer (float selected_filament_nbr = -1;)
2)manually load filament T0 to the nozzle. Ready to print
3)start printing

When the printer first receives the T command I get this:

because selected_filament_nbr = -1 tool change process is started.
but when unloading filament
```
 idler_select_filament_nbr(selected_filament_nbr);
 move_extruder(-MSU_BOWDEN_TUBE_LENGTH * steps_per_mm_correction_factor, MSU_SPEED, MSU_EXTRUDER_NBR);
```
I get the idler moving to position -1 (parking), because selected_filament_nbr =-1.

then moving the idelr to the required position of the new filament
```
idler_select_filament_nbr(index);
selected_filament_nbr = index;
move_extruder(MSU_BOWDEN_TUBE_LENGTH * steps_per_mm_correction_factor, MSU_SPEED, MSU_EXTRUDER_NBR);
```
and I get a collision in merger, because previous filament was not unloaded.

the next tool changes will be without problems

rozhkovets, 2024-09-01:
`how do you set the idler position?`
if the previous print was successfully completed, then the idler is already in the parking position. I just manually push the T0 filament and perform cleaning. I push the T1-4 filaments to the input into the mixer, with the expectation that there is no blockage when changing the tool.
`Using the move idler option on the LCD`
if the previous print was a failure or a jam occurred when changing the tool, then yes, only LCD control will help return everything to its original state.

anyway, i set "float selected_filament_nbr=0", and now msu will always think that t0 is loaded, cleaned and ready, t1-4 are ready, and idler is parked. Now i am responsible for the print preparation process (loads, additional cleanings, branding of tips, etc.)

`Manual load`
manual loading option is necessary, especially if the line from msu to extruder is not separable (I have no problems with this, everything is easily separated). I can experiment with this.

I think we don't need to consider that filaments are unloaded or missing at "selected_filament_nbr=-1" because we can't check it in code (no separate filament sensors). We can only make print preparation more convenient and leave everything else to the user, that's the price of cheapness.

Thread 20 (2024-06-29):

Move pulley body pivot point up to allow for the use of typical bed springs

PierreMasselot1, 2024-06-29:
Will provide performance and quality of life improvements:

- Better pressure control
- Cheaper and more easily accessible springs
- Will allow for easy idler disengagement (more useful than one would think when doing maintenance/fixing a jam)

PierreMasselot1, 2024-06-29:
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

Current progress

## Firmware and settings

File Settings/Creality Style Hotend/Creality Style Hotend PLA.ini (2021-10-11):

[filament:Creality Style Hotend PLA]
bed_temperature = 60
bridge_fan_speed = 30
chamber_temperature = 0
compatible_printers = 
compatible_printers_condition = 
compatible_prints = 
compatible_prints_condition = 
cooling = 1
disable_fan_first_layers = 3
end_filament_gcode = "; Filament-specific end gcode \n;END gcode for filament\n"
external_perimeter_fan_speed = -1
extrusion_multiplier = 1
fan_always_on = 1
fan_below_layer_time = 60
filament_colour = #29B2B2
filament_cooling_final_speed = 10
filament_cooling_initial_speed = 10
filament_cooling_moves = 1
filament_cooling_zone_pause = 0
filament_cost = 0
filament_density = 0
filament_deretract_speed = nil
filament_diameter = 1.75
filament_dip_extraction_speed = 90
filament_dip_insertion_speed = 90
filament_enable_toolchange_part_fan = 1
filament_enable_toolchange_temp = 1
filament_load_time = 12
filament_loading_speed = 14
filament_loading_speed_start = 19
filament_max_speed = 0
filament_max_volumetric_speed = 0
filament_max_wipe_tower_speed = 0
filament_melt_zone_pause = 0
filament_minimal_purge_on_wipe_tower = 15
filament_notes = ""
filament_ramming_parameters = "120 100 6.53226 6.64516 6.70968 6.74194 6.85484 6.91935 6.85484 7.51613 10.0645 13.5 15.3387 14.9516 13.5161 12.0645 11.1129 10.7581| 0.05 6.49249 0.45 6.69249 0.95 6.74623 1.45 6.93442 1.95 7.97949 2.45 14.957 2.95 14.3848 3.45 11.4387 3.95 10.686 4.45 9.6 4.95 7.37419"
filament_retract_before_travel = nil
filament_retract_before_wipe = nil
filament_retract_layer_change = nil
filament_retract_length = nil
filament_retract_lift = nil
filament_retract_lift_above = nil
filament_retract_lift_below = nil
filament_retract_restart_extra = nil
filament_retract_speed = nil
filament_settings_id = "Creality Style Hotend PLA"
filament_shrink = 100%
filament_skinnydip_distance = 47
filament_soluble = 0
filament_spool_weight = 0
filament_toolchange_delay = 0
filament_toolchange_part_fan_speed = 50
filament_toolchange_temp = 160
filament_type = PLA
filament_unload_time = 12
filament_unloading_speed = 80
filament_unloading_speed_start = 120
filament_use_fast_skinnydip = 0
filament_use_skinnydip = 1
filament_vendor = (Unknown)
filament_wipe = nil
filament_wipe_advanced_pigment = 0.5
filament_wipe_extra_perimeter = nil
first_layer_bed_temperature = 60
first_layer_temperature = 180
full_fan_speed_layer = 0
inherits = 
max_fan_speed = 30
max_speed_reduction = 90%
min_fan_speed = 30
min_print_speed = 10
slowdown_below_layer_time = 5
start_filament_gcode = "; Filament gcode\n"
temperature = 180
top_fan_speed = -1

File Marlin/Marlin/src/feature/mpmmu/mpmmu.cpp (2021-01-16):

#include "../../inc/MarlinConfig.h"
#if ENABLED(MMU_CLONE)

#include "mpmmu.h"
#include "../../MarlinCore.h"
#include "../../gcode/gcode.h"
#include "../../module/planner.h"
#include "../../module/motion.h"
#include "../../module/stepper.h"
#include "../../gcode/parser.h"
#include "../../module/endstops.h"
#if ENABLED(SERVO_IDLER)
  #include "../../module/servo.h"
#endif

float idlerPosition;
float offsetEndstopTo1 = 0.3 * 4.16;          //space from the endstop to the first bearing position(Filament 1)
float servopos1=20;//first bearing position
float servobearingangle=25;//space between each bearings
bool homingIdler=false;
float spaceBetweenBearings = 0.75 * 4.16;     //space in between each bearing
float parkedPosition = 0; //this is the parked position. when using the servo it will be the parked position in degree
float absolutePosition;                       //position for the idler to be pressing on the correct filament
float MMUToNozzleLength = BOWDEN_TUBE_LENGTH; //length, for now the unit is arbitrary but will have to set correct step per mm to get it in mm or scale acordingly
float storeExtruderPosition;
xyze_pos_t position;
#if ENABLED(SERVO_IDLER)
  Servo servoidler;
#endif
bool servoinit=false;

void MPMMU::tool_change(uint8_t index)
{
  #if ENABLED(SERVO_IDLER)
  if(!servoinit)
  idler_servo_init();
  servoinit=true;
  #endif
  position= current_position;
  storeExtruderPosition = planner.position.e;
  apply_motion_limits(position);
  planner.position.resetExtruder(); //reset the extruder position to 0 to avoid problems with next move
  //unload filament slow
  position.e= -10;
  planner.buffer_line(position, 4, MMU_EXTRUDER_PIN);
#ifdef DIRECT_DRIVE
  planner.position.resetExtruder();
  position.e= -10;
  planner.buffer_line(position, 4, EXTRUDER_PIN);
#endif
 
  position.e= -MMUToNozzleLength;
  planner.buffer_line(position,  16, MMU_EXTRUDER_PIN);
  planner.position.resetExtruder();
  
#ifdef DIRECT_DRIVE
  position.e= -MMUToNozzleLength;
  planner.buffer_line(position , 16, EXTRUDER_PIN);
#endif
  planner.synchronize();
  planner.position.resetExtruder();

  //idler select new filament
  #if ENABLED(SERVO_IDLER)
  servoidler.write(servopos1+index*servobearingangle);
  #else
  absolutePosition = offsetEndstopTo1 + index * spaceBetweenBearings;
  position.e=-(absolutePosition - idlerPosition);
  planner.buffer_line(position,  2, MMU_IDLER_PIN);
  planner.synchronize();
  planner.position.resetExtruder();
  #endif

  //reload the new filament slow
  position.e=10;
  planner.buffer_line(position, 4, MMU_EXTRUDER_PIN);
  planner.position.resetExtruder();
#ifdef DIRECT_DRIVE
  position.e=10;
  planner.buffer_line(position, 10, 4, EXTRUDER_PIN);
  planner.position.resetExtruder();
#endif
  //reload the new filament fast
  position.e=MMUToNozzleLength;
  planner.buffer_line(position, 16, MMU_EXTRUDER_PIN);
  planner.position.resetExtruder();
#ifdef DIRECT_DRIVE
  position.e=MMUToNozzleLength;
  planner.buffer_line(position, 16, EXTRUDER_PIN);
  planner.position.resetExtruder();
#endif
  planner.synchronize();
  planner.position.resetExtruder();
  idlerPosition = absolutePosition;
  planner.position.e = storeExtruderPosition;
//if direct drive is enabled park the idler leting the filament move freely through the MMU
#ifdef DIRECT_DRIVE
#if ENABLED(SERVO_IDLER)
  servoidler.write(parkedPosition);
#else
  absolutePosition = parkedPosition;
  position.e=-(absolutePosition - idlerPosition);
  planner.buffer_line(position,  2, MMU_IDLER_PIN);
  planner.synchronize();
  planner.position.resetExtruder();
#endif
#endif
}

void MPMMU::idler_home()
{
#if ENABLED(SERVO_IDLER)
  mpmmu.idler_servo_init();
#else
  homingIdler = true;
  endstops.enable(true);
  position= current_position;
  //apply_motion_limits(position);
  planner.position.resetExtruder();
  position.e= 100;
  planner.buffer_line(position, 1, MMU_IDLER_PIN); //move towards endstop until it's hit
  planner.synchronize();                                                    //wait for the move to finish
  endstops.validate_homing_move();
  homingIdler = false;              //homing completed
  idlerPosition = 0;                //new idler position
  planner.position.resetExtruder(); //reset the extruder position to 0 to avoid problems with next move
  endstops.not_homing();
#endif
  
}
#if ENABLED(SERVO_IDLER)
void MPMMU::idler_servo_init(){
  servoidler.attach(SERVO_IDLER_PIN);
  servoidler.write(parkedPosition);
}
#endif
bool MPMMU::idler_is_moving()
{
  return homingIdler;
}

#endif

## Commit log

2020-10-15 physical models (almost no testing & calibration)
    draft version of the physical models these are not meant to be printed, they haven't been tested and are far from being final.
    [Merger.step, mmu2-idler-body.scad, mmu2-idler.scad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]
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2020-11-08 scad reupload to test stl conversion
    small modifications in idler-body but not final yet
    [mmu2-idler-body.scad]
2020-11-08 New merger
    separated from the main body to allow for better printing and closer filament input for a smoother transition.
    [Merger V5.f3d]
2020-11-08 removed wrong directory structure
    [Merger V5.f3d]
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2020-11-10 merger fix
    [Merger_V6.f3d]
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2020-11-18 moved the code inside this repository for simplicity
    [Configuration.h, Configuration_adv.h]
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2020-12-09 ground work for direct drive support
    put bowden as the predefined state, fixed one of the comments so that
    enabling bowden doesn't require the addition of a //
    [Configuration.h]
2020-12-13 modified the model to fit the new idler body
    Cleaned up the model(close some holes caused by the increased bearing
    size where the bearing join with the endstop cut. I also shortened the
    "shaft" at the end of the idler since the new idler and pulley body
    change the alignement and the idler is pushed more torwards the extruder
    motor side.
    A second version had aslo been added in order to support heated inserts
    instead of nuts
    [mmu2-idler-heated-inserts.scad, mmu2-idler.scad]
2020-12-15 removed version # and increased tube clearance for the merger
    [MMU_Assembly.f3d, Merger.f3d, Merger_V6.f3d]
2020-12-15 Switched the endstop side and fixed/improved the model
    Put the endstop on the other side, the original one was wrong. Adjusted
    the "idler pressure" by that I mean how much the idler pushes against
    the filament, had to reduce it. Added some cable rounting channels this
    is just a try and proper cable management will be added in the future
    [MMU_Assembly.f3d]
2020-12-16 fixed idler spacing
    [MMU_Assembly.f3d]
2020-12-20 prevent idler disable
    [Configuration.h, Configuration_adv.h]
2020-12-24 code cleanup and simplification. Untested
    I realised that the switch inside the toolchange function didn't really
    bring anything since all of our cases are rather similar. I also created
    a separate function for the idler homing since a lot of stuff is going
    to be added there and I want to keep the code easy to understand. This
    has not been tested yet since I don't have access to my 3d printer right
    now but I still pushed the change since it will be way easier to work
    off of and I really didn't change anything so if I didn't make any
    mistakes it should work just fine.
    [mpmmu.cpp]
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2020-12-26 ground work for rotary encoder (unfinished and untested)
    [Configuration.h]
2020-12-27 bugfix for multimaterial print using prusa slicer
    [mpmmu.cpp]
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2020-12-27 over-extrude during filament load fix [untested]
    [mpmmu.cpp]
2020-12-30 removed config files[not up to date]
    removed the config files for the SKR Pro because they where hard to keep
    track off and you board config will vary depending on your printer setup
    so it doesn't make any sense to have it available
    [Configuration.h, Configuration_adv.h]
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2021-01-06 idler body reinforcements
    [MMU_Assembly.f3d]
2021-01-06 removed duplicate files, these were remodeled and modified in Fusion 360
    [mmu2-idler-body.scad, mmu2-pulley-body.scad]
2021-01-06 reduced filet to have more print bed contact for the endstop
    [MMU_Assembly.f3d]
2021-01-08 New idler in F360
    remodeled the idler in fusion 360 so that we don't have to deal with
    OpenSCAD files that are a nightmare. This is necessary in order to be
    easly able to modify the idler and add a servo mounted option which
    would increase board compatibility
    [mmu2-idler-heated-inserts.f3d]
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2021-01-08 fixed hole spacing for nema 17
    [MMU_Assembly.f3d]
2021-01-09 idler homing in G28 and no longer handled at tool change
    [mpmmu.cpp]
2021-01-10 added idler to assembly and fixed bearing spacing
    [MMU_Assembly.f3d, mmu2-idler-heated-inserts.f3d]
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2021-01-11 fixed the bug fix
    [mpmmu.cpp]
2021-01-11 fix over extrusion on restart
    [mpmmu.cpp]
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2021-01-14 fixed small bugs, removed unwanted servo write command
    [mpmmu.cpp]
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2021-01-18 fixed enstop spacing and idler mirroring error
    [MMU_Assembly.f3d, mmu2-idler-heated-inserts.f3d]
2021-01-18 fixed enstop spacing and idler mirroring error STEP
    [MSU assembly.step, mmu2-idler-heated-inserts.step]
2021-01-18 fixed wall and changed name
    [MMU_Assembly.f3d, MSU assembly.step, MSU_Assembly.f3d]
2021-01-18 fixed rod length in documentation
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2021-01-19 metal rod larger clearance
    [MSU_Assembly.f3d]
2021-01-19 better idler body hole and deeper heated inserts in the idler to fit M3x12 screws
    [MSU_Assembly.f3d]
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2021-01-20 Renamed to MSU and readability improvments
    I changed a lot of the configs in order to match the name of the device,
    this way there is no confusion between the actual MMU2 and this upgrade,
    which are getting further and further apart the more progress we make.
    [Configuration.h, Configuration_adv.h]
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2021-01-20 fixed the cold extrusion error on moves involving the idler
2021-01-21 Idler in assembly file and idler fix
    [MSU assembly.step, MSU_Assembly.f3d, mmu2-idler-heated-inserts.f3d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]
2021-01-21 better motor shaft clearance
    [MSU assembly.step, MSU_Assembly.f3d]
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2021-01-23 Reupload because of parts missing
    [MSU assembly.step, MSU_Assembly.f3d]
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2021-01-26 Partial implementation of the calibration process
    A couple of bug fixes and code polishing needed to be done.
    Not yet implemented but we have the functions ready for extruder moves
    to align the filament with the nozzle and then an empty menu that will
    be replaced with something to edit the BOWDEN_TUBE_LENGHT varirable
    defined in the config file. This will be helpful to do all the testing
    and the flashing the firmware once the correct value has been found.
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2021-01-26 extra clearance for the switch
    [MSU assembly.step, MSU_Assembly.f3d]
2021-01-27 better clearance metal rods
    [MSU assembly.step, MSU_Assembly.f3d]
2021-01-28 tighter shaft clearance
    [MSU assembly.step, MSU_Assembly.f3d]
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2021-01-28 mount hole fix
    [MSU mount.f3d, MSU mount.step, mount 1.stl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]
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2021-01-31 updated the menu, added calibration menu[few bugs remaining]
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2021-02-02 better bearing clearance and added the adapter to fit the 5mm rod
    [MSU assembly.step, MSU_Assembly.f3d]
2021-02-02 idler 0.7mm closer to the bearings: increased pressure and pressure tweaking
    [MSU_Assembly.f3d]
2021-02-04 disabled bowden lenght calibration to allow merge with main while keeping good stability
2021-02-05 Moved the shaft bearing back and updated all files
    all the fix required to get a good pressure on all the filaments. This
    is done by increasing the rigidity in the extruder shaft assembly and by
    puting the idler lower meaning that a lot more pressure can be applied
    if necessary
    [Idler body stepper motor.stl, MSU assembly.step, MSU_Assembly.f3d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]
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2021-02-09 higher pressure, better spring hole and tensioning, stronger
    [Idler body servo.stl, Idler body stepper motor.stl]
2021-02-09 moved the screws to give clearance to the bearing
    [Idler for stepper.stl]
2021-02-09 filament pressure fix
    [MSU assembly.step, MSU_Assembly.f3d]
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2021-02-11 merged filamentPressureFix and added clearance to switch the gear orientation and be able to properly connect the shaft with a solid coupler
    [MSU assembly.step, MSU_Assembly.f3d, pulley body.stl]
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2021-02-13 fix image link to display idler springs
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2021-02-18 extruder pin renaming fix
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2021-02-19 Added config option for linked direct drive setup
    [Configuration.h]
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2021-02-19 prevent disable incative extruder
    [Configuration_adv.h]
2021-02-19 idler servo bettter alignement with bearing and idler
    [Idler body servo.stl, MSU assembly.step, MSU_Assembly.f3d]
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2021-02-20 Added filament chip compartment, noise reduction
    After a certain amount of extrusion the filament can sometimes leave
    some bits of plastic inside the MSU, those don't cause any problems but
    they can become jammed between one of the gears and the pully body, with
    this modification we have extra space to keep them away from the gears
    and to prevent any grinding noises.
    TODO: figure out a way to get them out of the MSU without having to
    remove the motor(this may already be possible but I haven't had time to
    test this change)
    [MSU assembly.step, MSU_Assembly.f3d, pulley body.stl]
2021-02-27 added chamfer to avoid elephant foot problems on the motor mount
    [pulley body.stl]
2021-02-28 added chamfer to help with elephant foot related problems and added holes to help with assembly
    [Idler body stepper motor.stl]
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2021-03-03 Added DD ptfe adapter folder+Ender 3 DD adapter
    [Ender_3_direct_drive_conversion_adapter.stl, ender_3_direct_drive_conversion_adapter.f3d, ender_3_direct_drive_conversion_adapter.step]
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2021-03-04 wrong file export for the adapter
    [Ender_3_direct_drive_conversion_adapter.stl, ender_3_direct_drive_conversion_adapter.step]
2021-03-04 DD adapter, better fit, motor mount cutout, PC4-M10 coupler to allow bowden tube to meet with extruder
    [ender_3_direct_drive_conversion_adapter.f3d, ender_3_direct_drive_conversion_adapter.step, ender_3_direct_drive_conversion_adapter.stl]
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2021-03-17 Extruder adapter direct drive: better clearance and added 2mm to the base to fit the ptfe coupler properly
    [ender_3_direct_drive_conversion_adapter.f3d, ender_3_direct_drive_conversion_adapter.step, ender_3_direct_drive_conversion_adapter.stl]
2021-03-18 Easier filament tip tuning
    Python script to isolate the ramming sequence and the following cooling
    moves, it should help with testing and proper tweaking of the ramming sequence and evaluate the required number of cooling moves. The provided stl files have the sole purpose of creating a small Gcod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
    [Body1.stl, Body2.stl]
2021-03-31 Disable endstop settings when using a servo motor
    [Configuration.h]
2021-04-06 Changed servo config [servo control fix]
    [Configuration.h]
2021-04-06 config error endstop should be defined when !servo
    [Configuration.h]
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2021-04-06 Correct control of the servo
2021-05-01 improved mounting system, pulley body slightly modified to allow mirrored mounts
    [MSU mount.f3d, MSU mount.step, MSU_assembly.step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]
2021-05-04 split in stepper config and servo config, pulley body with mounts for new merger
    [MSU_assembly.step]
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2021-05-04 New Merger
    this is a new merger. The choice to mount it back on the MSU was made
    for simplicity and realiability. Most of the clogs happened at the
    coupler level since the connection from ptfe tubing to the 3d printed tubing
    can't be perfect meaning that attaching it directly to the pulley body
    allows the use of a single coupler on the MSU side of things allowing
    for less resistance. Furthermore, based on testing it seems that lining
    the plastic tubes with PTFE doesn't necesarly improve the amount of
    friction inside the merger and tends to increase it due to the added
    complexity of the design and the bridging point from PTFE to regular 3D
    printed material. This also helps reclaim entirely th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
    [Merger_V2.f3d, Merger_V2.step]
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2021-05-04 Merger alignment fix, more compact, less supports
    [Merger_V2.f3d, Merger_V2.step]
2021-05-04 more aggressive fillet on pulley body for easier assembly and file name changes(removed all spaces)
    [Idler body servo.stl, Idler body stepper motor.stl, Idler for servo.stl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]
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2021-05-05 Merger: more build plate contact, less supports, less friction
    [Merger_V2.f3d, Merger_V2.step]
2021-05-05 Merger, more aggresive hole size corection on the Z axis
    [Merger_V2.f3d, Merger_V2.step]
2021-05-06 filament flow sensor merger, spring loaded mounting system and wheel, work in progress
    [Merger_with_filament_flow_sensor_[WIP].f3d, Merger_with_filament_flow_sensor_[WIP].step]
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2021-05-11 filament flow sensor, bigger wheel, closer to filament
    [Merger_with_filament_flow_sensor_[WIP].f3d, Merger_with_filament_flow_sensor_[WIP].step]
2021-05-11 filament path vertical hole correction
    [pulley_body.stl]
2021-05-13 Servo idler body: stronger, easier to print, better looks
    [Idler_body_servo.stl, MSU_assembly.step]
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2021-05-13 merger fixation system and slightly more clearance
    [Merger_V2.f3d, Merger_V2.step, pulley_body.stl]
2021-05-14 filament sensor error handling
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2021-05-19 servo setup bug fix
2021-05-22 servo bugfix 2
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2021-05-22 Remove Marlin(to be replaced with separate fork)
    [Configuration.h, Configuration_adv.h]
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2021-05-23 Removed old merger
    removed the old merger since the new merger has been tested and works much better.
    [Merger.f3d, Merger.step, Merger_V2.f3d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]
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2021-05-26 Fixed merger hole
    [Merger.f3d, Merger.step, Merger.stl]
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2021-06-09 Additional merger design with better correction
    [Merger_2.0.stl, Merger_2.1.stl]
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2021-06-09 merger multiple clearance options (TODO add extra options)
    [Merger_2.0.stl, Merger_2.1.stl, Merger_2.1_Clearance_0.35_mm.stl]
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2021-06-19 horizontal expansion correction on output
    [Merger_2.1_Clearance_0.5_mm.stl]
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2021-08-14 :bug: bug fix for idler position loss
2021-08-15 Update Marlin bugfix
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2021-08-23 assembly small idler fix
    [MSU_assembly.step]
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2021-08-25 track correct branch
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2021-10-08 tighter clearance between merger and pulley body
    [Merger.stl]
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2022-01-06 flip teardrop shaped holes on idler body
    [Idler_body_servo.stl]
2022-01-06 idler body small gap fix
    [Idler_body_servo.stl]
2022-01-20 reinforced merger
    [Merger.stl]
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2022-03-13 idler bigger tolerances
    [Idler.stl]
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2022-07-19 Change python script, update README.MD with changes, and add example … (#9)
    * Change python script, update README.MD with changes, and add example image
    * change folder name, cleanup code
    * FilamentTipTesting: simpler code, indicate optional elements in readme
    [Body1.stl, Body2.stl]
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2023-09-01 move back to metal rod through pulley body and idler body
    while printing this mechanism allowed for a cheaper BOM, after some wear and tear too much flex appears, moving back to the old design.
    [Direct_mount_pulley_body.stl, Idler_body.stl, MSU_mount_pulley_body.stl]
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2023-09-06 Larger bearing clearances
    [Idler.stl]
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2023-09-08 new mount system, better press fit idler, redesign everything cuz Fusion 360 is :dog: :shit:
    [Direct_mount_pulley_body.stl, Idler.stl, Idler_body.stl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]
2023-09-08 idler fix 2nd bearing clearance
    [Idler.stl]
2023-09-09 idler better clearances
    [Idler.stl]
2023-09-09 tighter clearances
    [Idler.stl]
2023-09-12 better clearances
    [Servo_holder.stl]
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2024-06-09 increase clearance for bearing press fit on idler
    Closes: https://github.com/PierreMasselot1/Material-Switching-Unit/issues/17
    [Idler.stl]
2024-07-01 WIP 605 idler, new pivot point, less parts
    still needs testing but very promising so far, easier to print and simpler assembly
    [Idler_605.stl, new_pivot_idler_body.stl, new_pivot_pulley_body.stl]
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2024-07-25 Reduce flex in idler body, higher extruder pressure
    [new_pivot_idler_body.stl]
2024-09-05 tighter servo mount
    [new_pivot_idler_body.stl]
